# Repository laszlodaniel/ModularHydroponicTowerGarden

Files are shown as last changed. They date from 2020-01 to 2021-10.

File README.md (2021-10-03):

# ModularHydroponicTowerGarden
A modular 3D-printable hydroponic tower garden with Arduino compatible water pump controller.

[Get one or two on Tindie!](https://www.tindie.com/products/19512/)

**3DPrint** ~~folder contains the STL-files to print tower parts.~~ [STL-files are hosted on Thingiverse](https://www.thingiverse.com/thing:3405964)

**Arduino** folder contains the source code and compiled binaries for the water pump controller written in Arduino IDE 1.8.12.

**GUI** folder contains the C# source code and compiled Windows binary for an external computer written in Visual Studio 2019.

**PCB** folder contains everything to manufacture and assemble the hardware. You can buy it on [Tindie.](https://www.tindie.com/products/19512/)

## Command Line Interface (CLI)

The water pump controller can be interfaced with the Arduino Serial Monitor, or any other Serial Monitor application, regardless of OS platform, to change its settings via text-based commands. The current GUI works on Windows OS only.

By default the Serial Monitor shows regular status updates:

```
...
-----------STATUS-----------
Service mode : disabled
  Water pump : on @ 80%
       Timer : 00:04:46 left
Temperatures
    external : 0.0°C
    internal : 0.0°C
----------------------------

-----------STATUS-----------
Service mode : disabled
  Water pump : on @ 80%
       Timer : 00:04:45 left
Temperatures
    external : 0.0°C
    internal : 0.0°C
----------------------------

-----------STATUS-----------
Service mode : disabled
  Water pump : on @ 80%
       Timer : 00:04:44 left
Temperatures
    external : 0.0°C
    internal : 0.0°C
----------------------------
...
```

To turn off regular status update display send this command:

```
status=0
```

The Serial Monitor reacts the following way to user inputs:

```
Input: status=0
Command: status
Value: 0
Result: regular status updates disabled.
```

With the command "help" a complete description is printed to the Serial Monitor on the available commands:

```
----------------------------------HELP---------------------------------
         help : print this description.
      restart : restart controller.
         info : print controller information.
servicemode=X : set service mode,
                X=0: disabled (default),
                X=1: enabled.
     status=X : print regular status updates,
                X=0: disabled,
                X=1: enabled (default).
  pumpspeed=X : set water pump speed in percents,
                X=0...100 [%].
     ontime=X : set water pump on-time in minutes,
                X=0...71582 [min],
                when set to 0 the water pump is permanently turned off.
    offtime=X : set water pump off-time in minutes,
                X=0...71582 [min],
                when set to 0 the water pump is permanently turned on.
tempsensors=X : set temperature sensor configuration,
                X=0: none (default),
                X=1: external,
                X=2: internal,
                X=3: both external and internal.
   tempunit=X : set temperature unit,
                X=1: Celsius (default),
                X=2: Fahrenheit,
                X=4: Kelvin.
    ntcbeta=X : set temperature sensor beta value in Kelvin,
                X=3950 [K] by default.
    pwmfreq=X : set water pump driver PWM frequency in Hertz,
                X=490 [Hz] by default.

Note: settings are automatically saved to the internal EEPROM.
-----------------------------------------------------------------------
```

To display controller information send the "info" command:

```
--------------------INFO---------------------
        AVR signature : 1E 95 0F (ATmega328P)
     Hardware version : V1.01
        Hardware date : 2019.11.18 18:07:36
        Assembly date : 2020.03.09 13:20:28
        Firmware date : 2021.04.20 14:02:43
         Service mode : disabled
     Water pump state : off
   Water pump on-time : 5 minute(s)
  Water pump off-time : 60 minute(s)
Temperature sensor(s) : external and internal
     Temperature unit : Celsius
       NTC beta value : 3950 K
        PWM frequency : 490 Hz
---------------------------------------------
```

## Pictures

MHTG empty

MHTG seedlings

MHTG halfway through

MHTG CAD drawing

MHTG planting module

V1.02 water pump controller

MHTG GUI 01

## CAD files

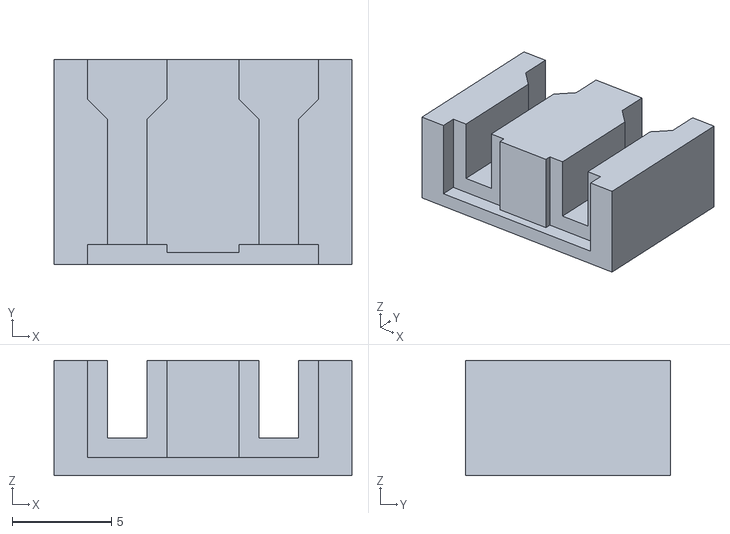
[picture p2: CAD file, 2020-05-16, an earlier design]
PCB/V102/MHTG_V102/box/MHTG_V102_LED_extender_fixture.STL
15.0 x 10.3 x 5.80

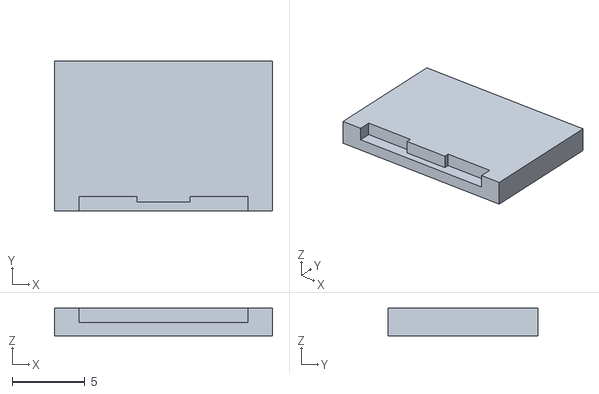
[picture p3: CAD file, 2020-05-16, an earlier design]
PCB/V102/MHTG_V102/box/MHTG_V102_LED_extender_cover.STL
15.0 x 10.3 x 1.90

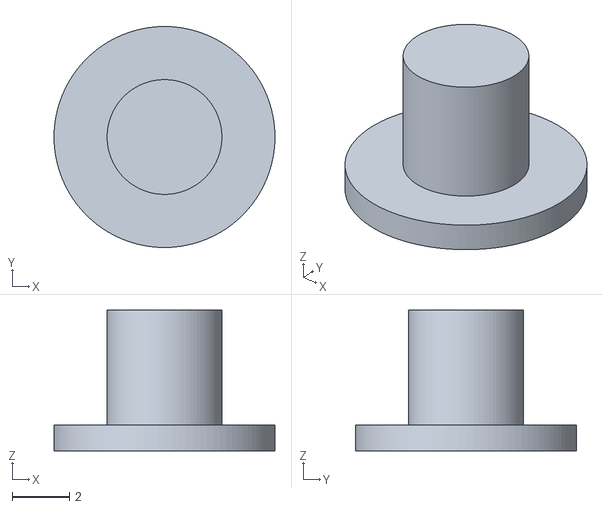
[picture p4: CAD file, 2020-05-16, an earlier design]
PCB/V102/MHTG_V102/box/MHTG_V101_reset_button.STL
7.70 x 7.70 x 4.90

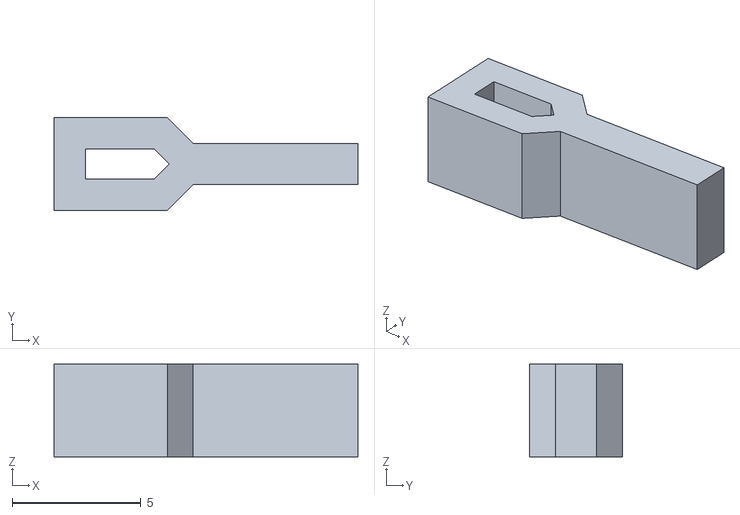
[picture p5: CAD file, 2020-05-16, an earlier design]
PCB/V102/MHTG_V102/box/MHTG_V101_LED_extender_transparent.STL
11.8 x 3.60 x 3.60

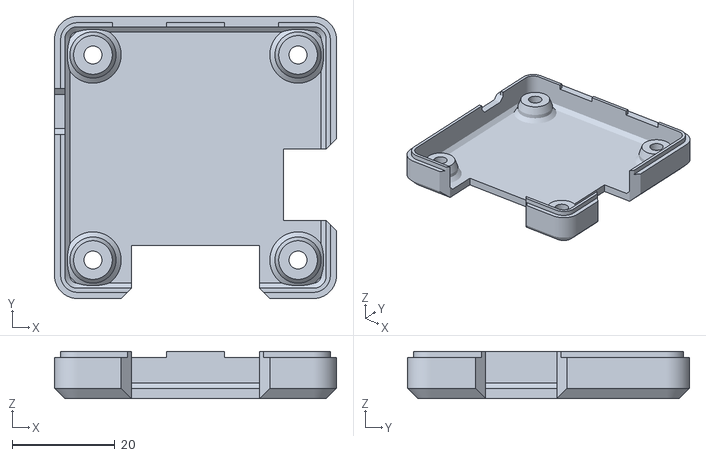
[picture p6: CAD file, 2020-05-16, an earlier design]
PCB/V102/MHTG_V102/box/MHTG_V102_PCB_box_bottom.STL
55.0 x 55.0 x 9.20

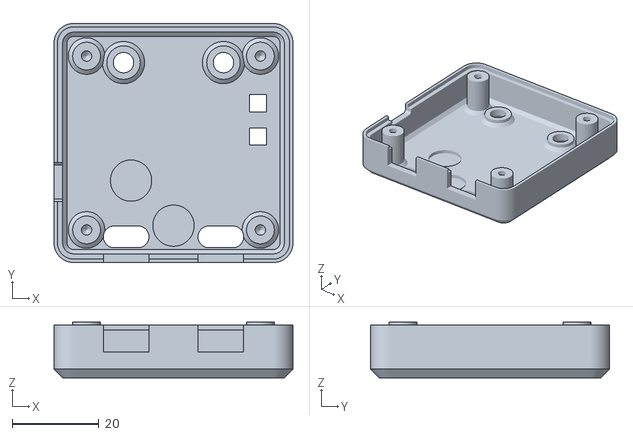
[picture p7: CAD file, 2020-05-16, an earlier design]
PCB/V102/MHTG_V102/box/MHTG_V102_PCB_box_top.STL
55.0 x 55.0 x 12.8

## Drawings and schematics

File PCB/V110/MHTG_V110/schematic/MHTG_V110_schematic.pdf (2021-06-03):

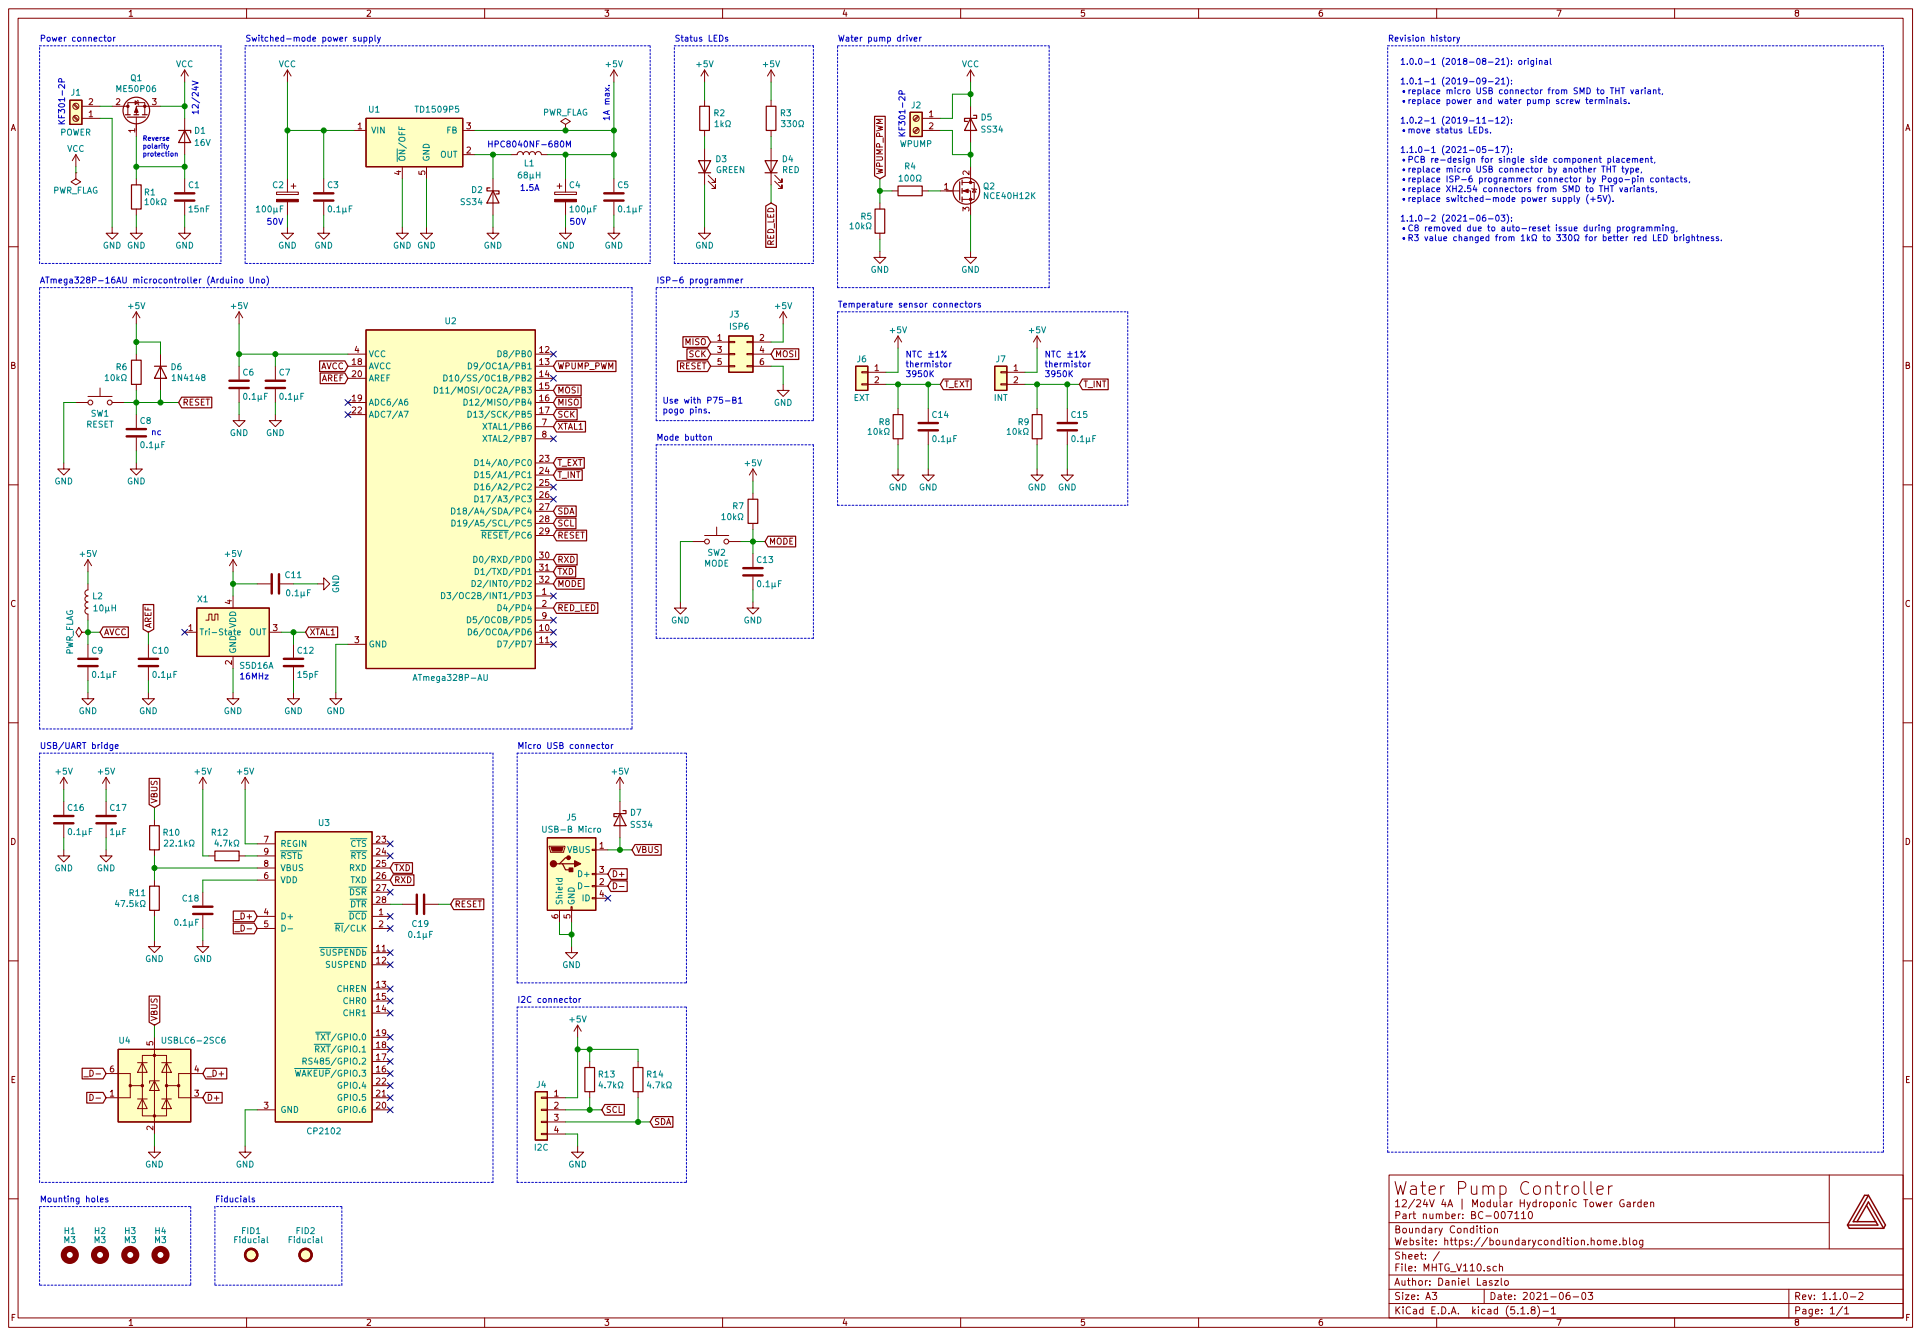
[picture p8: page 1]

Switched-mode power supply

replace micro USB connector from SMD to THT variant,
replace power and water pump screw terminals.

PCB re-design for single side component placement,
replace micro USB connector by another THT type,
replace ISP-6 programmer connector by Pogo-pin contacts,
replace XH2.54 connectors from SMD to THT variants,
replace switched-mode power supply (+5V).

C8 removed due to auto-reset issue during programming,
R3 value changed from 1k to 330 for better red LED brightness.

Water Pump Controller
12/24V 4A | Modular Hydroponic Tower Garden
File: MHTG_V110.sch Sheet: / Boundary Condition Author: Daniel Laszlo Website: https://boundarycondition.home.blog Part number: BC-007110

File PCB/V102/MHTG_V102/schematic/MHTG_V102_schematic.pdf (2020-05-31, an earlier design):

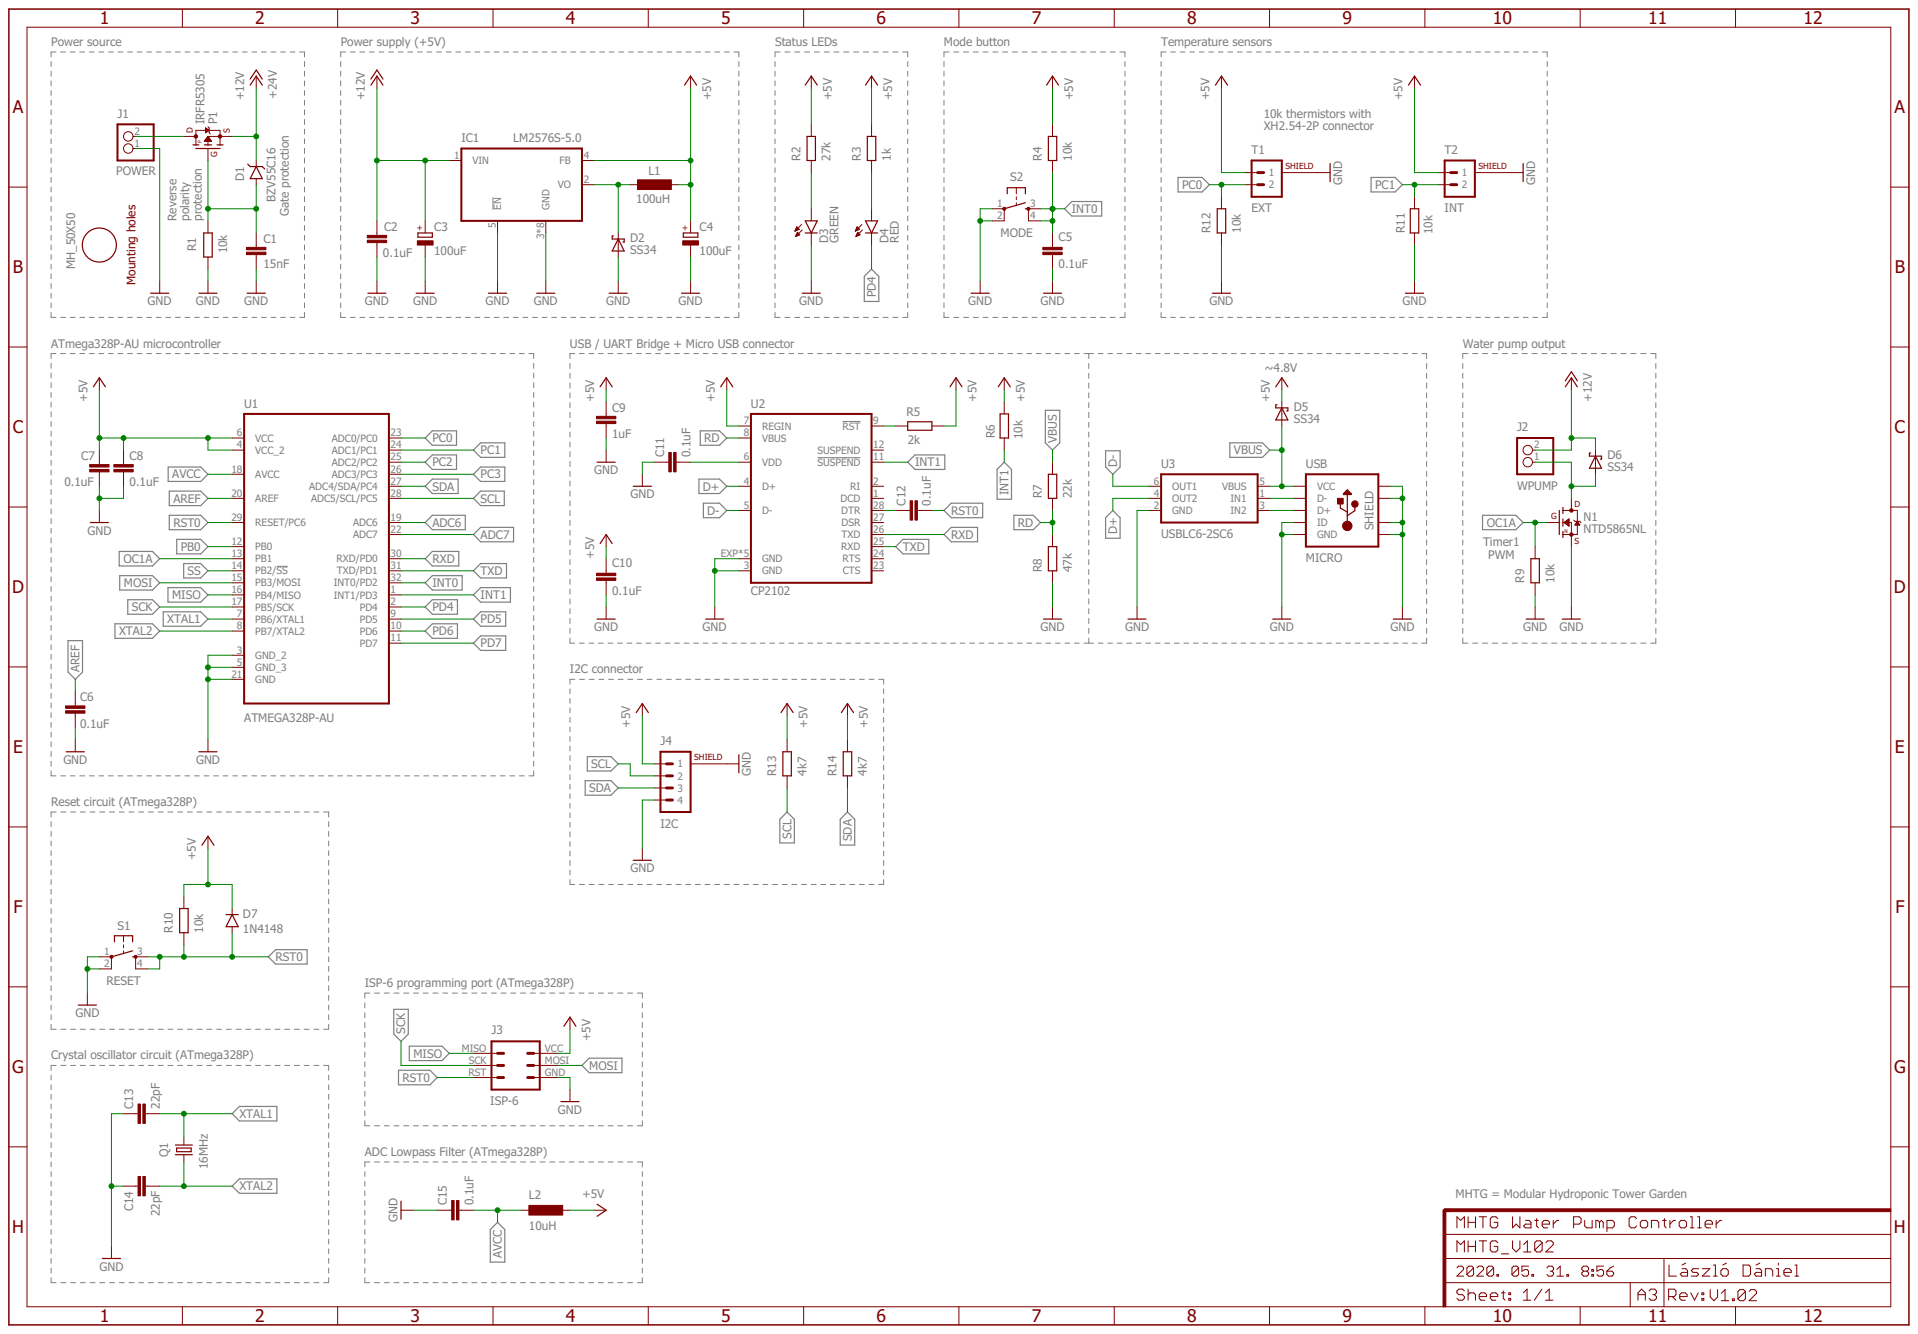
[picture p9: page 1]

Power supply (+5V) | | Status LEDs

MHTG = Modular Hydroponic Tower Garden

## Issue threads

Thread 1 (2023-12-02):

Thingiverse link not working

faleandroid, 2023-12-02:
simply i would like to know if it's possibile to have the stl files to print, since the thingiverse link is no more reachable.

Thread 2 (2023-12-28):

Thingiverse Link not Working

duartejm, 2023-12-28:
Hi Daniel, first of all thank you for all the effort regarding this project!
I would like to ask you, if you decided to delete the Thingiverse account or if you moved it to another platform?
I was able to download all the STL files for this project, however, in Thingiverse there were already a lot of remixes that I cannot find since your page is not accessible. Do you know if it is possible to see these remixes?

Once again, thank you for your effort on this project!

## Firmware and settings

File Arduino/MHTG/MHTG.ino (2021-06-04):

/*
 * ModularHydroponicTowerGarden (https://github.com/laszlodaniel/ModularHydroponicTowerGarden)
 * Copyright (C) 2021, Daniel Laszlo
 *
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
 * You should have received a copy of the GNU General Public License
 * along with this program. If not, see <http://www.gnu.org/licenses/>.
 */

#include <avr/io.h>
#include <avr/boot.h>
#include <avr/interrupt.h>
#include <avr/wdt.h>
#include <math.h>
#include <util/atomic.h>
#include <EEPROM.h>
#include <LiquidCrystal_I2C.h> // https://github.com/fdebrabander/Arduino-LiquidCrystal-I2C-library
#include <TimeLib.h> // https://github.com/PaulStoffregen/Time
#include <TimerOne.h> // https://github.com/PaulStoffregen/TimerOne
#include <Wire.h>


// Firmware date/time of compilation in 64-bit UNIX time
// https://www.epochconverter.com/hex
#define FW_DATE 0x0000000060BA2885

#define TEMP_EXT      A0 // external 10k NTC thermistor is connected to this analog pin
#define TEMP_INT      A1 // internal 10k NTC thermistor is connected to this analog pin
#define RED_LED_PIN   4  // red LED
#define WATERPUMP_PIN 9  // waterpump pwm output

// Set (1), clear (0) and invert (1->0; 0->1) bit in a register or variable easily
#define sbi(reg, bit) (reg) |=  (1 << (bit))
#define cbi(reg, bit) (reg) &= ~(1 << (bit))
#define ibi(reg, bit) (reg) ^=  (1 << (bit))

#define to_uint16(hb, lb) (uint16_t)(((uint8_t)hb << 8) | (uint8_t)lb)
#define to_uint32(msb, hb, lb, lsb) (uint32_t)(((uint32_t)msb << 24) | ((uint32_t)hb << 16) | ((uint32_t)lb << 8) | (uint32_t)lsb)

// Packet related stuff
// DATA CODE byte building blocks
// Commands (low nibble (4 bits))
#define reset               0x00
#define handshake           0x01
#define status              0x02
#define settings            0x03
#define request             0x04
#define response            0x05
// 0x06-0x0D reserved
#define debug               0x0E
#define ok_error            0x0F

// SUB-DATA CODE byte
// Command 0x0F (ok_error)
#define ok                                      0x00
#define error_length_invalid_value              0x01
#define error_datacode_invalid_command          0x02
#define error_subdatacode_invalid_value         0x03
#define error_payload_invalid_values            0x04
#define error_packet_checksum_invalid_value     0x05
#define error_packet_timeout_occured            0x06
// 0x06-0xFD reserved
#define error_eeprom_checksum_mismatch          0xFC
#define error_not_enough_mcu_ram                0xFD
#define error_internal                          0xFE
#define error_fatal                             0xFF

// Construct an object called "lcd" for the external display (optional)
LiquidCrystal_I2C lcd(0x27, 20, 4);

// Variables
uint32_t Ve, Vi; // raw analog voltage readings (external, internal temperatures)
uint16_t beta = 3950; // thermistor specific value
float inv_beta = 1.00 / (float)beta; // reciprocal of beta used in calculations
float inv_t0 = 1.00 / 298.15; // reciprocal of t0 = normal room temperature
uint16_t update_interval = 1000; // milliseconds

float T_ext[3]; // calculated external temperatures (0: Kelvin, 1: Celsius, 2: Fahrenheit)
float T_int[3]; // calculated internal temperatures (0: Kelvin, 1: Celsius, 2: Fahrenheit)
uint8_t temperature_payload[8];

uint32_t current_millis = 0;
uint8_t current_timestamp[4]; // current time is stored here when "update_timestamp" is called
uint32_t last_update_millis = 0;
uint32_t last_wpump_millis = 0;
uint32_t remaining_time = 0;
uint8_t percent_left = 0;
uint32_t t = 0; // remaining time is seconds
uint8_t h, m, s; // calculated from "t": hours component (h), minutes component (m), seconds component (s)

char rxBuffer[32]; // buffer for text-based communication
uint8_t rxBufferPtr = 0;

// EEPROM settings
uint8_t eeprom_content[64];
uint8_t default_eeprom_content[64] =
{
    0x00, 0xC7, 0x00, 0x00, 0x00, 0x00, 0x00, 0x00, 0x00, 0x00, 0x00, 0x00, 0x00, 0x00, 0x00, 0x00,
    0x00, 0x00, 0x7F, 0x00, 0x0D, 0xBB, 0xA0, 0x00, 0x0D, 0xBB, 0xA0, 0x00, 0x01, 0x0F, 0x6E, 0x01,
    0xEA, 0x00, 0x00, 0x00, 0x00, 0x00, 0x00, 0x00, 0x00, 0x00, 0x00, 0x00, 0x00, 0x00, 0x00, 0x00,
    0x00, 0x00, 0x00, 0x00, 0x00, 0x00, 0x00, 0x00, 0x00, 0x00, 0x00, 0x00, 0x00, 0x00, 0x00, 0x00
};

uint8_t hw_version[2] = { 0x00, 0x00 };
uint8_t hw_date[8] = { 0x00, 0x00, 0x00, 0x00, 0x00, 0x00, 0x00, 0x00 };
uint8_t assembly_date[8] = { 0x00, 0x00, 0x00, 0x00, 0x00, 0x00, 0x00, 0x00 };
uint8_t old_wpump_pwm = 0;
uint8_t wpump_pwm = 0; // 0: 0% - 255: 100%
uint32_t wpump_ontime = 0; // 900000 milliseconds = 900 seconds = 15 minutes
uint32_t wpump_offtime = 0; // 900000 milliseconds = 900 seconds = 15 minutes
uint8_t enabled_temperature_sensors = 0;
uint8_t temperature_unit = 0;
uint16_t pwm_frequency = 490; // Hz
uint8_t calculated_checksum = 0;
bool checksum_ok = false;

bool wpump_on = true;
uint32_t wpump_interval = 0;
uint8_t avr_signature[3];

volatile bool mode_button_pressed = false;
bool autoupdate = true;
bool ascii_mode = true;
bool service_mode = false;
uint16_t service_mode_blinking_interval = 500; // ms
uint16_t led_blink_duration = 50; // ms
uint32_t previous_led_blink = 0; // ms
uint32_t red_led_ontime = 0; // ms

// Packet related variables
// Timeout values for packets
uint8_t command_timeout = 100; // milliseconds
uint16_t command_purge_timeout = 200; // milliseconds, if a command isn't complete within this time then delete the usb receive buffer
uint8_t ack[1] = { 0x00 }; // acknowledge payload array
uint8_t err[1] = { 0xFF }; // error payload array
uint8_t ret[1]; // general array to store arbitrary bytes

// LCD related variables
// Custom LCD-characters
// https://maxpromer.github.io/LCD-Character-Creator/
uint8_t degree_symbol[8] = { 0x06, 0x09, 0x09, 0x06, 0x00, 0x00, 0x00, 0x00 }; // °
uint8_t progress_bar_1[8] = { 0x00, 0x00, 0x10, 0x10, 0x10, 0x00, 0x00, 0x00 };
uint8_t progress_bar_2[8] = { 0x00, 0x00, 0x18, 0x18, 0x18, 0x00, 0x00, 0x00 };
uint8_t progress_bar_3[8] = { 0x00, 0x00, 0x1C, 0x1C, 0x1C, 0x00, 0x00, 0x00 };
uint8_t progress_bar_4[8] = { 0x00, 0x00, 0x1E, 0x1E, 0x1E, 0x00, 0x00, 0x00 };
uint8_t progress_bar_5[8] = { 0x00, 0x00, 0x1F, 0x1F, 0x1F, 0x00, 0x00, 0x00 };

typedef union {
    float number;
    uint8_t bytes[4];
} FLOATUNION_t;


/*****************************************************************************
Function: get_temps()
Purpose:  measures and converts the analog voltage present on A0 and A1 pins
Note:     -
******************************************************************************/
void get_temps(float *te, float *ti)
{
    float Ke, Ce, Fe; // external temperature variables
    float Ki, Ci, Fi; // internal temperature variables
    uint16_t sampleCount = 512;

    Ve = 0; // start with zero
    Vi = 0; // start with zero

    for (uint16_t i = 0; i < sampleCount; i++) // measure analog voltage quickly 500 times and add results together
    {
        Ve += analogRead(TEMP_EXT);
    }

    for (uint16_t i = 0; i < sampleCount; i++) // measure analog voltage quickly 500 times and add results together
    {
        Vi += analogRead(TEMP_INT);
    }

    Ve /= sampleCount; // calculate average value
    Vi /= sampleCount; // calculate average value

    // Calculate external temperature using this equation involving the thermistor's beta property
    Ke = 1.0 / (inv_t0 + inv_beta * (log(1023.0 / (float)Ve - 1.0))); // Kelvin
    Ce = Ke - 273.15; // Celsius
    Fe = Ce * 1.8 + 32.0; // Fahrenheit

    // Calculate internal temperature using this equation involving the thermistor's beta property
    Ki = 1.0 / (inv_t0 + inv_beta * (log(1023.0 / (float)Vi - 1.0))); // Kelvin
    Ci = Ki - 273.15; // Celsius
    Fi = Ci * 1.8 + 32.0; // Fahrenheit

    // Save values in the input arrays
    te[0] = Ke;
    te[1] = Ce;
    te[2] = Fe;

    ti[0] = Ki;
    ti[1] = Ci;
    ti[2] = Fi;

    // Save float values as their 4-byte constituents
    switch (temperature_unit)
    {
        case 1: // Celsius
        {
            FLOATUNION_t ext_celsius;
            FLOATUNION_t int_celsius;
            ext_celsius.number = te[1];
            int_celsius.number = ti[1];
            temperature_payload[0] = ext_celsius.bytes[0];
            temperature_payload[1] = ext_celsius.bytes[1];
            temperature_payload[2] = ext_celsius.bytes[2];
            temperature_payload[3] = ext_celsius.bytes[3];
            temperature_payload[4] = int_celsius.bytes[0];
            temperature_payload[5] = int_celsius.bytes[1];
            temperature_payload[6] = int_celsius.bytes[2];
            temperature_payload[7] = int_celsius.bytes[3];
            break;
        }
        case 2: // Fahrenheit
        {
            FLOATUNION_t ext_fahrenheit;
            FLOATUNION_t int_fahrenheit;
            ext_fahrenheit.number = te[2];
            int_fahrenheit.number = ti[2];
            temperature_payload[0] = ext_fahrenheit.bytes[0];
            temperature_payload[1] = ext_fahrenheit.bytes[1];
            temperature_payload[2] = ext_fahrenheit.bytes[2];
            temperature_payload[3] = ext_fahrenheit.bytes[3];
            temperature_payload[4] = int_fahrenheit.bytes[0];
            temperature_payload[5] = int_fahrenheit.bytes[1];
            temperature_payload[6] = int_fahrenheit.bytes[2];
            temperature_payload[7] = int_fahrenheit.bytes[3];
            break;
        }
        case 4: // Kelvin
        {
            FLOATUNION_t ext_kelvin;
            FLOATUNION_t int_kelvin;
            ext_kelvin.number = te[0];
            int_kelvin.number = ti[0];
            temperature_payload[0] = ext_kelvin.bytes[0];
            temperature_payload[1] = ext_kelvin.bytes[1];
            temperature_payload[2] = ext_kelvin.bytes[2];
            temperature_payload[3] = ext_kelvin.bytes[3];
            temperature_payload[4] = int_kelvin.bytes[0];
            temperature_payload[5] = int_kelvin.bytes[1];
            temperature_payload[6] = int_kelvin.bytes[2];
            temperature_payload[7] = int_kelvin.bytes[3];
            break;
        }
        default: // Celsius
        {
            FLOATUNION_t ext_celsius;
            FLOATUNION_t int_celsius;
            ext_celsius.number = te[1];
            int_celsius.number = ti[1];
            temperature_payload[0] = ext_celsius.bytes[0];
            temperature_payload[1] = ext_celsius.bytes[1];
            temperature_payload[2] = ext_celsius.bytes[2];
            temperature_payload[3] = ext_celsius.bytes[3];
            temperature_payload[4] = int_celsius.bytes[0];
            temperature_payload[5] = int_celsius.bytes[1];
            temperature_payload[6] = int_celsius.bytes[2];
            temperature_payload[7] = int_celsius.bytes[3];
            break;
        }
    }
    
} // end of get_temps


/*****************************************************************************
Function: handle_mode_button()
Purpose:  sets a flag when the mode button is pressed
Note:     the loop-function processes this flag
******************************************************************************/
void handle_mode_button(void)
{
    ATOMIC_BLOCK(ATOMIC_FORCEON)
    {
        mode_button_pressed = true;
    }
    
} // end of handle_mode_button


/*****************************************************************************
Function: change_wpump_speed()
Purpose:  gradually changes water pump speed from current to target value
Note:     it's easier on the power supply if the speed is changed slowly
******************************************************************************/
void change_wpump_speed(uint8_t new_wpump_pwm)
{
    if (wpump_on || service_mode)
    {
        if (new_wpump_pwm == 0)
        {
            Timer1.pwm(WATERPUMP_PIN, 0); // turn off water pump
            digitalWrite(RED_LED_PIN, HIGH); // turn off indicator LED
            old_wpump_pwm = 0;
            return;
        }
        
        // Gradually change from old speed to new speed
        if (new_wpump_pwm > old_wpump_pwm) // increase speed
        {
            for (uint16_t i = old_wpump_pwm; i <= new_wpump_pwm; i++)
            {
                Timer1.pwm(WATERPUMP_PIN, map(i, 0, 255, 0, 1023)); // 8-bit to 10-bit conversion is necessary for this library
                delay(15);
                wdt_reset();
            }
        }
        else if (new_wpump_pwm < old_wpump_pwm) // decrease speed
        {
            for (uint16_t i = old_wpump_pwm; i >= new_wpump_pwm; i--)
            {
                Timer1.pwm(WATERPUMP_PIN, map(i, 0, 255, 0, 1023)); // 8-bit to 10-bit conversion is necessary for this library
                delay(15);
                wdt_reset();
            }
        }
    
        digitalWrite(RED_LED_PIN, LOW); // turn on indicator LED
        old_wpump_pwm = new_wpump_pwm; // save last set pwm-level
    }
    
} // end of change_wpump_speed


/*****************************************************************************
Function: update_timestamp()
Purpose:  saves the current elapes milliseconds in the target byte-array
Note:     -
******************************************************************************/
void update_timestamp(uint8_t *target)
{
    uint32_t mcu_current_millis = millis();
    target[0] = (mcu_current_millis >> 24) & 0xFF;
    target[1] = (mcu_current_millis >> 16) & 0xFF;
    target[2] = (mcu_current_millis >> 8) & 0xFF;
    target[3] = mcu_current_millis & 0xFF;
    
} // end of update_timestamp


/*****************************************************************************
Function: read_avr_signature()
Purpose:  read AVR device signature bytes into an array given in the parameter
Note:     ATmega328P: 1E 95 0F
******************************************************************************/
void read_avr_signature(uint8_t *target)
{
    target[0] = boot_signature_byte_get(0x0000);
    target[1] = boot_signature_byte_get(0x0002);
    target[2] = boot_signature_byte_get(0x0004);

} // end of read_avr_signature


/*************************************************************************
Function: update_pwm_frequency()
Purpose:  change water pump driver PWM-frequency
Note:     frequency changing while the water pump is running may cause glitches
**************************************************************************/
void update_pwm_frequency(uint16_t frequency)
{
    uint16_t period = 1000000 / frequency; // microseconds
    Timer1.setPeriod(period);
    
} // end of update_pwm_frequency


/*****************************************************************************
Function: update_settings()
Purpose:  takes values from the temporary eeprom_content array and updates variables
Note:     -
******************************************************************************/
void update_settings(void)
{
    hw_version[0] = eeprom_content[0x00];
    hw_version[1] = eeprom_content[0x01];
    hw_date[0] = eeprom_content[0x02];
    hw_date[1] = eeprom_content[0x03];
    hw_date[2] = eeprom_content[0x04];
    hw_date[3] = eeprom_content[0x05];
    hw_date[4] = eeprom_content[0x06];
    hw_date[5] = eeprom_content[0x07];
    hw_date[6] = eeprom_content[0x08];
    hw_date[7] = eeprom_content[0x09];
    assembly_date[0] = eeprom_content[0x0A];
    assembly_date[1] = eeprom_content[0x0B];
    assembly_date[2] = eeprom_content[0x0C];
    assembly_date[3] = eeprom_content[0x0D];
    assembly_date[4] = eeprom_content[0x0E];
    assembly_date[5] = eeprom_content[0x0F];
    assembly_date[6] = eeprom_content[0x10];
    assembly_date[7] = eeprom_content[0x11];
    wpump_pwm = eeprom_content[0x12];
    wpump_ontime = to_uint32(eeprom_content[0x13], eeprom_content[0x14], eeprom_content[0x15], eeprom_content[0x16]);
    wpump_offtime = to_uint32(eeprom_content[0x17], eeprom_content[0x18], eeprom_content[0x19], eeprom_content[0x1A]);
    enabled_temperature_sensors = eeprom_content[0x1B];
    temperature_unit = eeprom_content[0x1C];
    beta = to_uint16(eeprom_content[0x1D], eeprom_content[0x1E]);
    inv_beta = 1.00 / (float)beta;
    pwm_frequency = to_uint16(eeprom_content[0x1F], eeprom_content[0x20]);
    update_pwm_frequency(pwm_frequency);

    if (!service_mode)
    {
        if ((wpump_ontime == 0) && (wpump_offtime == 0))
        {
            wpump_interval = 0;
            change_wpump_speed(0);
            wpump_on = false;
        }
        else
        {
            if (wpump_offtime == 0) // permanently turn on water pump
            {
                wpump_interval = 0;
                wpump_on = true;
                change_wpump_speed(wpump_pwm);
            }
    
            if (wpump_ontime == 0) // permanently turn off water pump
            {
                wpump_interval = 0;
                change_wpump_speed(0);
                wpump_on = false;
            }
    
            if ((wpump_ontime != 0) && (wpump_offtime != 0))
            {
                if (wpump_on)
                {
                    wpump_interval = wpump_ontime;
                    wpump_on = true;
                    update_pwm_frequency(pwm_frequency);
                    change_wpump_speed(wpump_pwm);
                }
                else
                {
                    wpump_interval = wpump_offtime;
                    change_wpump_speed(0);
                    wpump_on = false;
                }
            }
        }
    }
    else
    {
        change_wpump_speed(0);
        wpump_on = false;
    }
    
} // end of update_settings


/*************************************************************************
Function: default_eeprom_settings()
Purpose:  sets default values in RAM when the EEPROM checksum doesn't match
Note:     -
**************************************************************************/
void default_eeprom_settings(void)
{
    // Calculate checksum for the default EEPROM content array
    default_eeprom_content[0x3F] = calculate_checksum(default_eeprom_content, 0, 63);

    // Copy all values
    for (uint8_t i = 0; i < 64; i++)
    {
        eeprom_content[i] = default_eeprom_content[i];
    }
    
} // end of default_eeprom_settings


/*************************************************************************
Function: read_eeprom_settings()
Purpose:  read internal EEPROM into RAM
Note:     -
**************************************************************************/
void read_eeprom_settings(void)
{
    // Read first 64 bytes of the internal EEPROM into RAM
    for (uint8_t i = 0; i < 64; i++)
    {
        eeprom_content[i] = EEPROM.read(i);
    }
    
    // Calculate expected checkum
    calculated_checksum = calculate_checksum(eeprom_content, 0, 63);

    if (calculated_checksum == eeprom_content[0x3F])
    {
        checksum_ok = true;
        update_settings(); // load and apply stored settings
    }
    else
    {
        checksum_ok = false;
        default_eeprom_settings(); // load default settings
        update_settings(); // apply default settings
        send_usb_packet(ok_error, error_eeprom_checksum_mismatch, err, 1);
    }
    
} // end of read_eeprom_settings
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
void loop()
{
    wdt_reset(); // reset watchdog timer to 0 seconds so no accidental restart occurs
    handle_usb_data();
    current_millis = millis(); // check current time

    if (((uint32_t)(current_millis - last_wpump_millis) >= wpump_interval) && (wpump_ontime != 0) && (wpump_offtime != 0)) // casting the time difference to uint32_t is a workaround for millis timer overflow that occurs every 50 days or so
    {
        last_wpump_millis = current_millis; // save the last time we were here
        
        if (wpump_on)
        {
            wpump_interval = wpump_offtime;
            change_wpump_speed(0); // set zero speed to turn off
            wpump_on = false;
        }
        else
        {
            wpump_on = true;
            wpump_interval = wpump_ontime;
            if (!service_mode) change_wpump_speed(wpump_pwm);
        }
    }

    if ((uint32_t)(current_millis - last_update_millis) >= update_interval) // casting the time difference to uint32_t is a workaround for millis timer overflow that occurs every 50 days or so
    {     
        last_update_millis = current_millis; // save the last time we were here
        get_temps(T_ext, T_int); // measure temperatures and save them in these arrays
        
        if (autoupdate) // update external devices regularly (USB, LCD)
        {
            update_status();
            lcd_update();
        }
    }

    if (mode_button_pressed) // handle mode-button press
    {
        mode_button_pressed = false; // re-arm

        if (!service_mode)
        {
            service_mode = true; // enter service mode
            
            if (wpump_on)
            {
                change_wpump_speed(0); // turn off water pump
            }
        }
        else
        {
            service_mode = false; // exit service mode

            if (wpump_on) // if water pump is on according to the timer
            {
                wpump_on = true;
                change_wpump_speed(wpump_pwm); // resume water pump activity
            }

            if (!wpump_on) digitalWrite(RED_LED_PIN, HIGH); // turn off red LED is this condition catches it during blinking
        }
    }

    if (service_mode) // blink red LED when in service mode
    {   
        if ((uint32_t)(current_millis - previous_led_blink) >= service_mode_blinking_interval)
        {
            if ((previous_led_blink - last_update_millis) != service_mode_blinking_interval) previous_led_blink = last_update_millis + service_mode_blinking_interval; // avoid blinking issues by shifting the blink start after Serial/LCD update
            else previous_led_blink = current_millis; // save current time
            digitalWrite(RED_LED_PIN, LOW); // turn on red LED
            red_led_ontime = current_millis; // save time when red LED was turned on
        }

        if ((uint32_t)(current_millis - red_led_ontime) >= led_blink_duration)
        {
            digitalWrite(RED_LED_PIN, HIGH); // turn off red LED
        }
    }
}

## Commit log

2020-01-13 Update
    Wrong subdata code fixed in (EEPROM write acknowledgement).
    [MHTG.ino]
2020-01-13 Update
    Temperature sensor disconnection is now recognized and readings are zeroed out on the affected channel. Basic I2C LCD support added.
2020-02-13 Update
    Corrected SS34 package value and added missing connectors (T1 and T2)
2020-02-13 Update
    Water pump speed is now changing gradually between selected speeds.
2020-02-13 Update
    Fixed a bug that turned on the water pump when it was in a timed off-state.
    [MHTG.ino]
2020-02-20 Update
    In Arduino code there are two helper defines that convert raw bytes to word (uint16) and double-word (uint32).
    GUI About form modified to always appear in the center of the main form.
2020-03-06 Update
    Whenever the on/off time is set to zero, the water pump stays on (off-time = 0) or stays off (on-time or on/off-time= 0).
    Service mode can be enabled by pressing the Mode button or selecting it in the GUI from the Tools menu. When in service mode the water pump is turned off regardless of its current state and the red L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
2020-03-06 Update README.md
    Added Thingiverse link to STL-files.
2020-03-11 Update
    Arduino:
    - allocated EEPROM area is increased from 32 bytes to 64 bytes,
    - new setting added: water pump driver PWM-frequency; a desired Hz-value is stored as an unsigned 16-bit integer; default value is 490 Hz; sometimes the water pump motor behaves better at higher frequencies (1000-2000 Hz). When the frequency is different than 490 Hz the code changes to phase- and frequency correct PWM mode.
    GUI:
    - Added PWM-frequency input textbox in the hidden Debug section.
    [MHTG.ino]
2020-03-15 Update
    - default analogWrite() function replaced with the TimerOne library counterpart. It allows fine PWM-frequency tuning and decent waveshaping,
    - added LCD functions to print useful information on a 20x4 character I2C LCD.
    - minor formatting changes.
    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
    [MHTG.ino]
2020-03-16 Update
    - timer display on the LCD tweaked to not show remaining time bigger than 99:59:59,
    - progress bar pecentage fixed at 100% when the water pump is set to constantly on/off state, in which case the timer shows "--:--:--".
    GUI: remaining time string formatting fixed to show bigger than 24 hours intervals.
    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
    [MHTG.ino]
2020-04-29 Update MHTG.ino
    Temperatures are compared to float values instead of integers.
2020-05-05 Fixed temperature display on LCD.
    Floating point numbers are a pain in the neck to handle in Arduino.
    [MHTG.ino]
2020-05-16 Add STL-files for 3D printed parts.
    [MHTG_V101_LED_extender_transparent.STL, MHTG_V101_reset_button.STL, MHTG_V102_LED_extender_cover.STL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]
2021-04-20 Implement Command Line Interface (CLI)
    The water pump controller can be interfaced with the Arduino Serial Monitor, or any other Serial Monitor application, regardless of OS platform, to change its settings via text-based commands. The cu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
2021-05-25 Add MHTG_V110 schematic files
2021-06-03 V110 schematic modified
    1.1.0-2 (2021-06-03):
    -C8 removed due to auto-reset issue during programming,
    -R3 value changed from 1kΩ to 330Ω for better red LED brightness.
2021-06-04 Various bugfixes
    - LED blinking interval changed from 100 ms to 50 ms,
    - LED blinking issue fixed when Mode button was pressed around the same time when Serial/LCD update was in progress,
    - improved temperature measurement and display, temperatures below -9.9°C/°F and above 99.9°C/°F/K are not displayed.
    [MHTG.ino]
2021-06-13 Remove Gerber files
    [MHTG_V102.drills.xln]

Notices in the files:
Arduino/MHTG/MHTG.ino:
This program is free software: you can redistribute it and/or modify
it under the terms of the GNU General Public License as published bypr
